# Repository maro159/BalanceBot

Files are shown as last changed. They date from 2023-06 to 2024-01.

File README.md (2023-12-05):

# BalanceBot

RPi Pico based self balancing robot developed as academic project on AGH UST

**NOTE:** This project is still WIP (Work In Progress)

## Overview
A goal was to create two-wheel robot with ability to self-balance. 

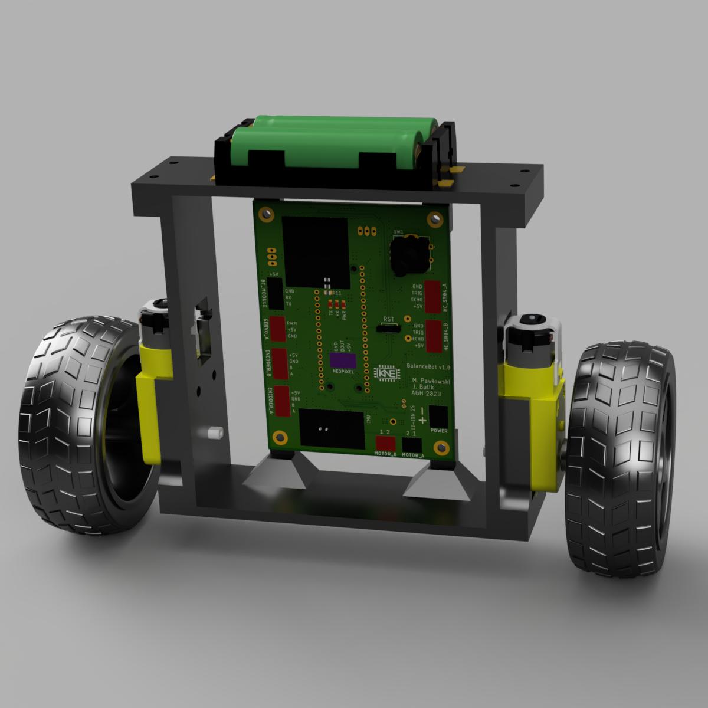
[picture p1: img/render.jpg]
render
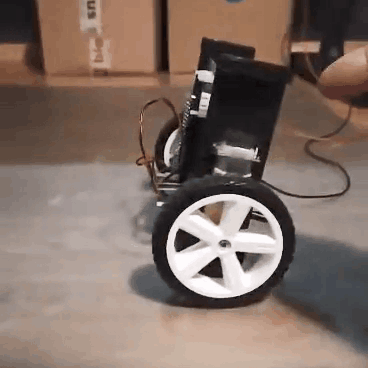
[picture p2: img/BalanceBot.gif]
gif
|  |  |
|-|-|

### Hardware
- 2S LiIon/LiPo battery pack
- custom PCB
- RPi Pico (dual core ARM Cortex M0+)
- DRV8833 H-Bridge (much more efficient than popular L293) 
- 2x DFRobot SJ01 120:1 DC Motor with magnetic encoder
- MPU-6050 6-axis IMU (accelerometer + gyroscope)
- 2x HC04 ultrasonic distance sensor
- SSD1306 OLED display + EC11 rotary encoder 

### Software
Code was written in C language using *Raspberry Pi Pico SDK*.

Self-stabilization algorithm is based on measuring vehicle's tilt angle using accelerometer and gyroscope measurements. The angle is calculated using *complementary filter*. Idea of the filter is to estimate angle avoiding errors from gyroscope low frequency components and accelerometer high frequency components.

Next stage of controller consists of 3-level cascade of PID controllers:

|name|set point|input|output|description|
|-|-|-|-|-|
|pid_speed|target_robot_speed|current_robot_speed|target_angle|calculate angle needed to reach target_robot_speed|
|pid_imu|target_angle|current_angle|target_motor_speed|calculate motor speed needed to reach target_angle|
|pid_motor_a|target_motor_speed|current_motor_a_speed|motor_a_power|calculate power (PWM duty cycle) needed to achieve current_motor_a_speed|
|pid_motor_b|target_motor_speed|current_motor_b_speed|motor_b_power|calculate power (PWM duty cycle) needed to achieve current_motor_b_speed|

This may seem little unintuitive on first sight, but makes robot able to balance "in place" instead of drifting to either side. Such algorithm was possible to implement thanks to motor encoders. Working principle is explained pretty well [on Husarion blog](https://medium.com/husarion-blog/fresh-look-at-self-balancing-robot-algorithm-d50d41711d58), where we got the idea from. Thanks a lot for publishing it!

PID coefficients can be set via OLED GUI, which can be navigated using rotary encoder. Big thanks to David Schramm for the [pico ssd1306 library](https://github.com/daschr/pico-ssd1306)

All of above runs on a single core. There is a plan to use second core for wireless communication and further expand abilities of the robot 

### PC App
There is a [python script](PC/main.py) included, which implements plotting data received on serial port. It is simple and unoptimized, but was really helpful during debugging and tuning of complementary filter and PID controllers.
 
## Further development
- design new frame to lower center of mass -> lower moment of inertia
- replace heavy 18650 LiIon battery pack with light LiPo 
- improve IMU measurements by using MPU-6050's interrupt
- fine-tune PIDs
- implement driving and remote control
- implement obstacle detection using ultrasonic sensors

## Attribution
- *slightly modified* [SSD1306 library by David Schramm](https://github.com/daschr/pico-ssd1306)
- idea of PID cascade from [husarion/self-balancing-telepresence-robot](https://github.com/husarion/self-balancing-telepresence-robot) and [Husarion Medium blog](https://medium.com/husarion-blog/fresh-look-at-self-balancing-robot-algorithm-d50d41711d58)

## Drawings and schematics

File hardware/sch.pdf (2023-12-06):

## IMU

# Power Supply

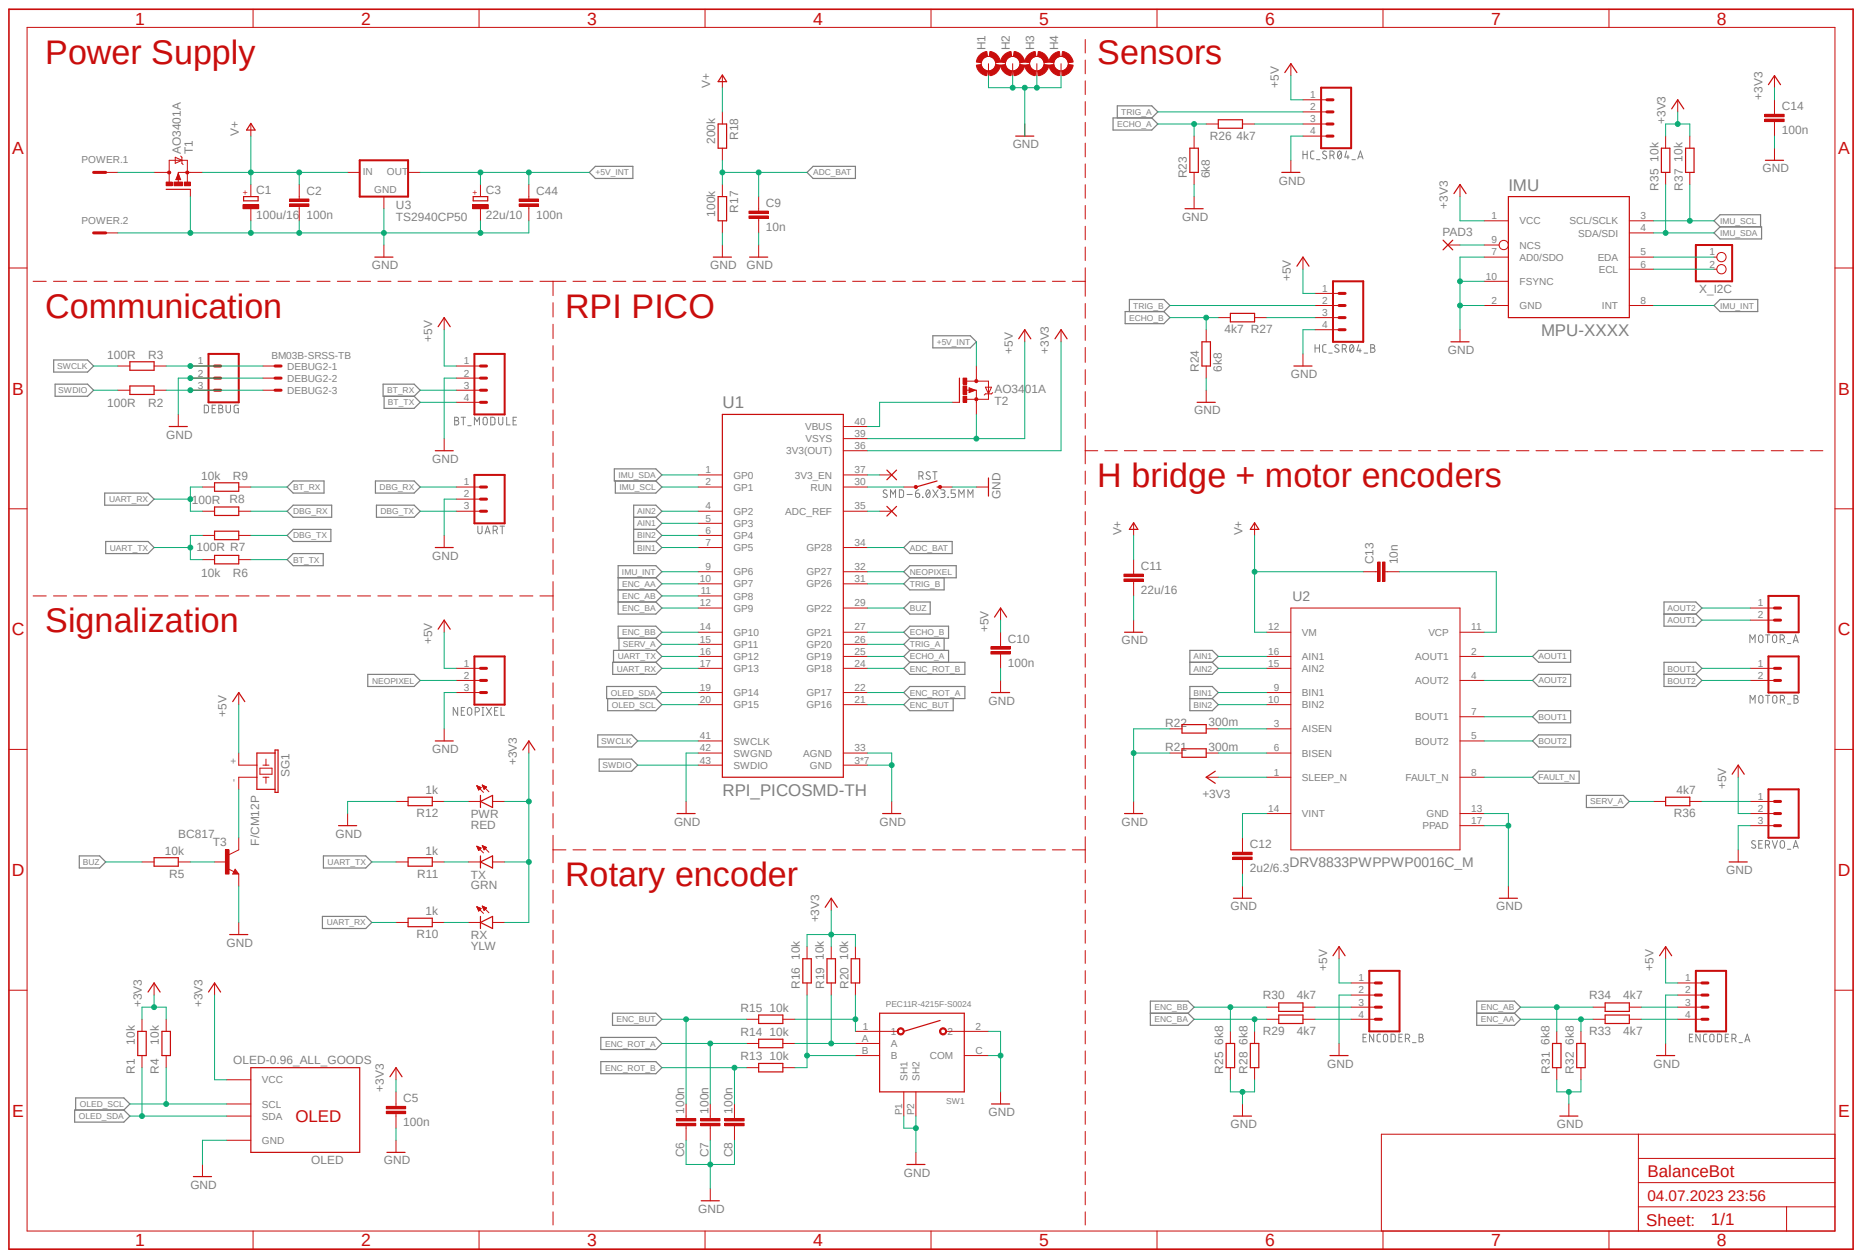
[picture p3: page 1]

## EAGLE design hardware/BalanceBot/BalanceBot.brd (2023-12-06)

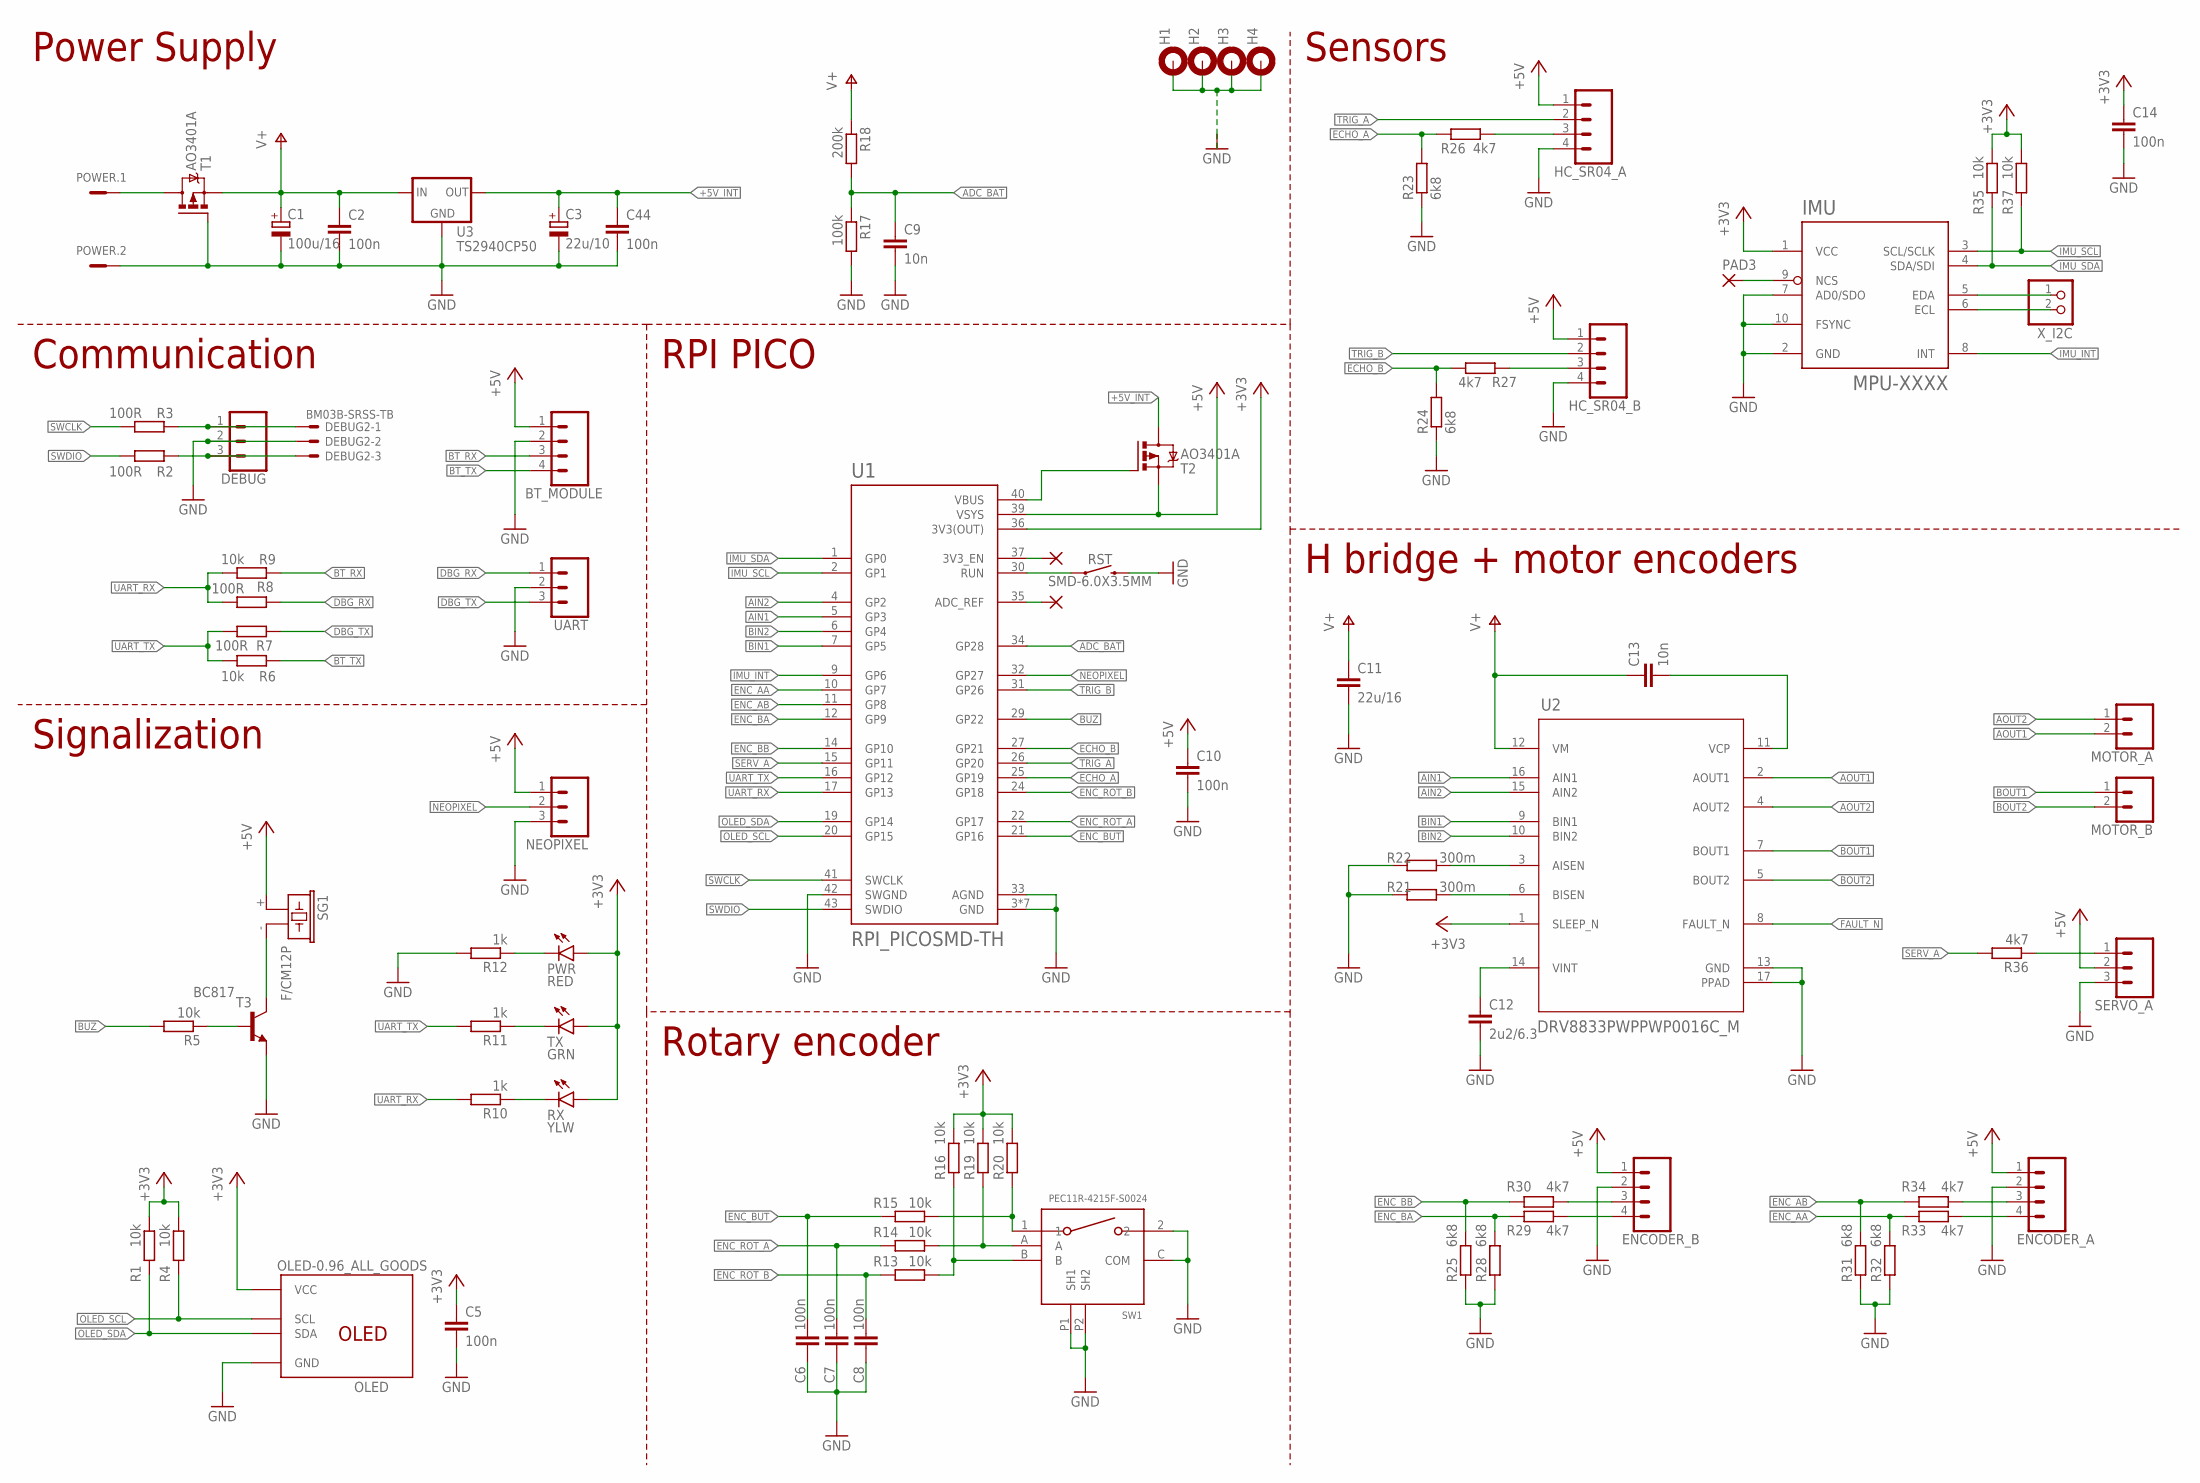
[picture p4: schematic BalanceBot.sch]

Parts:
BT_MODULE: JST-XH-04-PIN-LONG-PAD; JST-XH-04-PACKAGE-LONG-PAD
C1: 100u/16; E2-5
C2, C5, C6, C7, C8, C10, C14, C44: 100n; C0805
C3: 22u/10; SMC_B
C9, C13: 10n; C0805
C11: 22u/16; C0805
C12: 2u2/6.3; C0805
DEBUG: JST-XH-03-PIN-LONG-PAD; JST-XH-03-PACKAGE-LONG-PAD
DEBUG2: BM03B-SRSS-TB
ENCODER_A: JST-XH-04-PIN-LONG-PAD; JST-XH-04-PACKAGE-LONG-PAD
ENCODER_B: JST-XH-04-PIN-LONG-PAD; JST-XH-04-PACKAGE-LONG-PAD
H1, H2, H3, H4: MOUNT-PAD-ROUND3.2; 3,2-PAD
HC_SR04_A, HC_SR04_B: JST-XH-04-PIN-LONG-PAD; JST-XH-04-PACKAGE-LONG-PAD
IMU: MPU-XXXX; MPUXXXX
MOTOR_A: JST-XH-02-PIN-LONG-PAD; JST-XH-02-PACKAGE-LONG-PAD
MOTOR_B: JST-XH-02-PIN-LONG-PAD; JST-XH-02-PACKAGE-LONG-PAD
NEOPIXEL: JST-XH-03-PIN-LONG-PAD; JST-XH-03-PACKAGE-LONG-PAD
OLED: OLED-0.96_ALL_GOODS; ALL_GOODS
PAD1, PAD2, PAD3: WIREPADSMD1,27-254; SMD1,27-2,54
POWER: MCV2
PWR: RED; CHIP-LED0805
R1, R4, R5, R6, R9, R13, R14, R15, R16, R19, R20, R35, R37: 10k; R0805
R2, R3, R7, R8: 100R; R0805
R10, R11, R12: 1k; R0805
R17: 100k; R0805
R18: 200k; R0805
R21, R22: 300m; R1206
R23, R24, R25, R28, R31, R32: 6k8; R0805
R26, R27, R29, R30, R33, R34, R36: 4k7; R0805
RST: SMD-6.0X3.5MM; TACTILE_SWITCH_SMD_6.0X3.5MM
RX: YLW; CHIP-LED0805
SERVO_A: JST-XH-03-PIN-LONG-PAD; JST-XH-03-PACKAGE-LONG-PAD
SG1: F/CM12P
SW1: PEC11R-4215F-S0024
T1, T2: AO3401A; SOT23
T3: BC817; SOT23-BEC
TX: GRN; CHIP-LED0805
U1: RPI_PICOSMD-TH; PICO-PKG-TH-ONLY
U2: DRV8833PWPPWP0016C_M; PWP0016C_M
U3: TS2940CP50; DPACK
UART: JST-XH-03-PIN-LONG-PAD; JST-XH-03-PACKAGE-LONG-PAD
X_I2C: PINHD-1X2; 1X02

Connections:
3V3_EN: PAD2.1, U1.37 (3V3_EN)
+3V3: C5.1, C14.1, IMU.1 (VCC), OLED.2 (VCC), PWR.A, R1.1, R4.1, R16.1, R19.1, R20.1, R35.1, R37.1, RX.A, TX.A, U1.36 (3V3(OUT)), U2.1 (SLEEP_N)
+5V: BT_MODULE.1, C10.1, ENCODER_A.1, ENCODER_B.1, HC_SR04_A.1, HC_SR04_B.1, NEOPIXEL.1, SERVO_A.2, SG1.+ (1), T2.2 (S), U1.39 (VSYS)
+5V_INT: C3.+, C44.1, T2.3 (D), U3.3 (OUT)
ADC_BAT: C9.1, R17.1, R18.2, U1.34 (GP28)
ADC_REF: PAD1.1, U1.35 (ADC_REF)
AIN1: U1.5 (GP3), U2.16 (AIN1)
AIN2: U1.4 (GP2), U2.15 (AIN2)
AOUT1: MOTOR_A.2, U2.2 (AOUT1)
AOUT2: MOTOR_A.1, U2.4 (AOUT2)
BIN1: U1.7 (GP5), U2.9 (BIN1)
BIN2: U1.6 (GP4), U2.10 (BIN2)
BOUT1: MOTOR_B.1, U2.7 (BOUT1)
BOUT2: MOTOR_B.2, U2.5 (BOUT2)
BT_RX: BT_MODULE.3, R9.1
BT_TX: BT_MODULE.4, R6.1
BUZ: R5.2, U1.29 (GP22)
DBG_RX: R8.1, UART.1
DBG_TX: R7.1, UART.3
ECHO_A: R23.2, R26.1, U1.25 (GP19)
ECHO_B: R24.2, R27.1, U1.27 (GP21)
ECL: IMU.6 (ECL), X_I2C.2
EDA: IMU.5 (EDA), X_I2C.1
ENC_AA: R32.2, R33.1, U1.10 (GP7)
ENC_AB: R31.2, R34.2, U1.11 (GP8)
ENC_BA: R28.2, R29.1, U1.12 (GP9)
ENC_BB: R25.2, R30.2, U1.14 (GP10)
ENC_BUT: C6.1, R15.1, U1.21 (GP16)
ENC_ROT_A: C7.1, R14.1, U1.22 (GP17)
ENC_ROT_B: C8.1, R13.1, U1.24 (GP18)
FAULT_N: U2.8 (FAULT_N)
GND: BT_MODULE.2, C1.-, C2.2, C3.-, C5.2, C6.2, C7.2, C8.2, C9.2, C10.2, C11.2, C12.2, C14.2, C44.2, DEBUG.2, DEBUG2.2, ENCODER_A.2, ENCODER_B.2, H1.B3,2, H2.B3,2, H3.B3,2, H4.B3,2, HC_SR04_A.4, HC_SR04_B.4, IMU.2 (GND), IMU.7 (AD0/SDO), IMU.10 (FSYNC), NEOPIXEL.3, OLED.1 (GND), POWER.2, R12.2, R17.2, R21.1, R22.1, R23.1, R24.1, R25.1, R28.1, R31.1, R32.1, RST.2, SERVO_A.3, SW1.2, SW1.C (COM), SW1.P1 (SH1), SW1.P2 (SH2), T1.1 (G), T3.E, U1.3 (GND), U1.8 (GND), U1.13 (GND), U1.18 (GND), U1.23 (GND), U1.28 (GND), U1.33 (AGND), U1.38 (GND), U1.42 (SWGND), U2.13 (GND), U2.17 (PPAD), U3.4 (GND), UART.2
IMU_INT: IMU.8 (INT), U1.9 (GP6)
IMU_SCL: IMU.3 (SCL/SCLK), R37.2, U1.2 (GP1)
IMU_SDA: IMU.4 (SDA/SDI), R35.2, U1.1 (GP0)
unnamed: R22.2, U2.3 (AISEN)
unnamed: R21.2, U2.6 (BISEN)
unnamed: C13.2, U2.11 (VCP)
unnamed: C12.1, U2.14 (VINT)
unnamed: POWER.1, T1.3 (D)
unnamed: PWR.C, R12.1
unnamed: R11.1, TX.C
unnamed: R15.2, R20.2, SW1.1
unnamed: R5.1, T3.B
unnamed: R14.2, R19.2, SW1.A
unnamed: SG1.- (2), T3.C
unnamed: R13.2, R16.2, SW1.B
unnamed: R10.1, RX.C
unnamed: HC_SR04_A.3, R26.2
unnamed: HC_SR04_B.3, R27.2
unnamed: ENCODER_A.3, R34.1
unnamed: ENCODER_A.4, R33.2
unnamed: ENCODER_B.3, R30.1
unnamed: ENCODER_B.4, R29.2
unnamed: DEBUG.1, DEBUG2.1, R3.1
unnamed: R36.1, SERVO_A.1
unnamed: DEBUG.3, DEBUG2.3, R2.2
NCS: IMU.9 (NCS), PAD3.1
NEOPIXEL: NEOPIXEL.2, U1.32 (GP27)
OLED_SCL: OLED.3 (SCL), R4.2, U1.20 (GP15)
OLED_SDA: OLED.4 (SDA), R1.2, U1.19 (GP14)
RUN: RST.1, U1.30 (RUN)
SERV_A: R36.2, U1.15 (GP11)
SWCLK: R3.2, U1.41 (SWCLK)
SWDIO: R2.1, U1.43 (SWDIO)
TRIG_A: HC_SR04_A.2, U1.26 (GP20)
TRIG_B: HC_SR04_B.2, U1.31 (GP26)
UART_RX: R8.2, R9.2, R10.2, U1.17 (GP13)
UART_TX: R6.2, R7.2, R11.2, U1.16 (GP12)
V+: C1.+, C2.1, C11.1, C13.1, R18.1, T1.2 (S), U2.12 (VM), U3.1 (IN)
VBUS: T2.1 (G), U1.40 (VBUS)

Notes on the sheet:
RPI PICO
Power Supply
Communication
Signalization
Rotary encoder
H bridge + motor encoders
Sensors

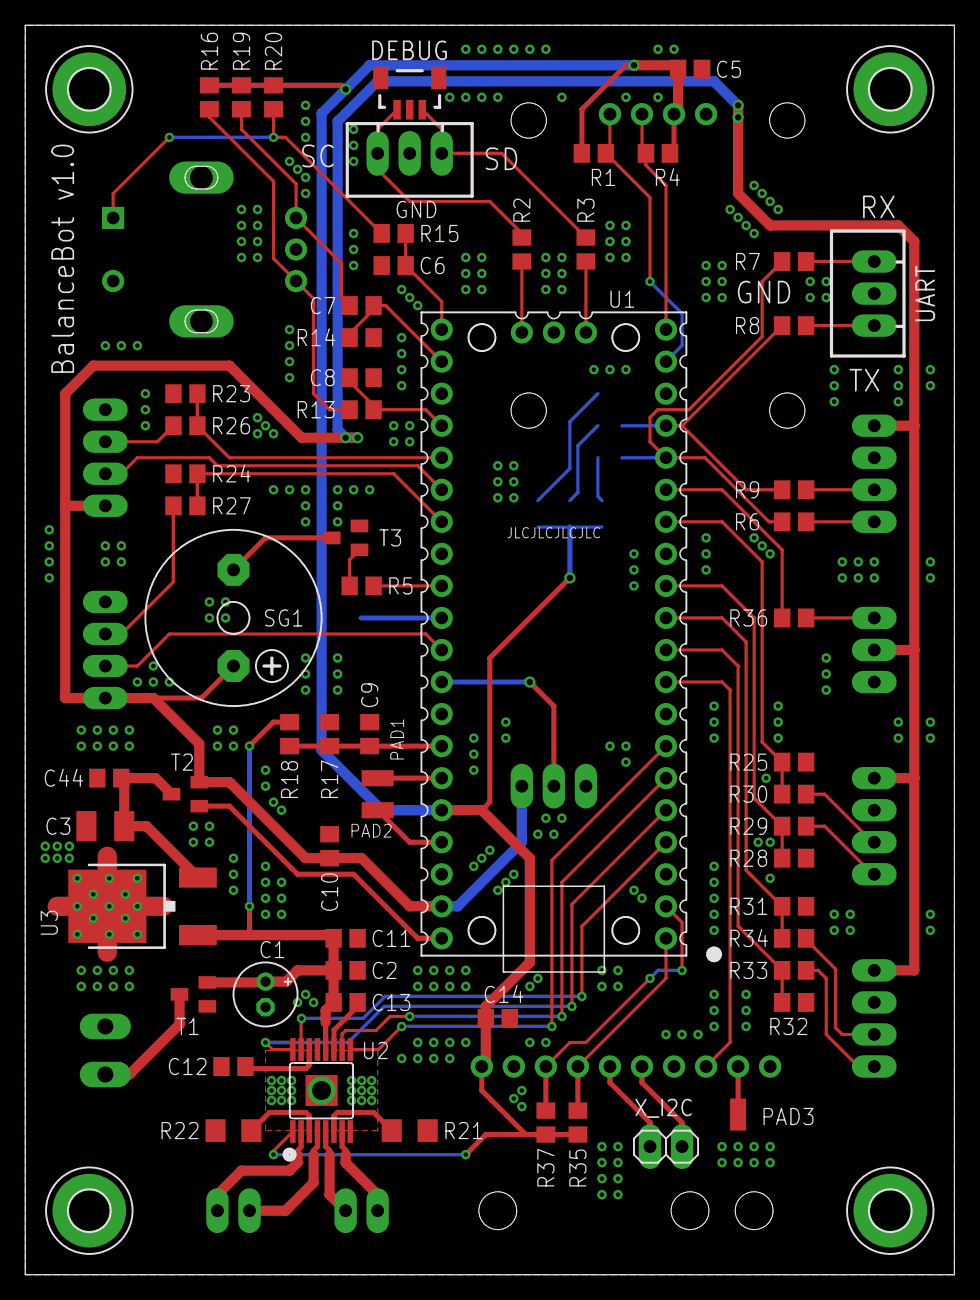
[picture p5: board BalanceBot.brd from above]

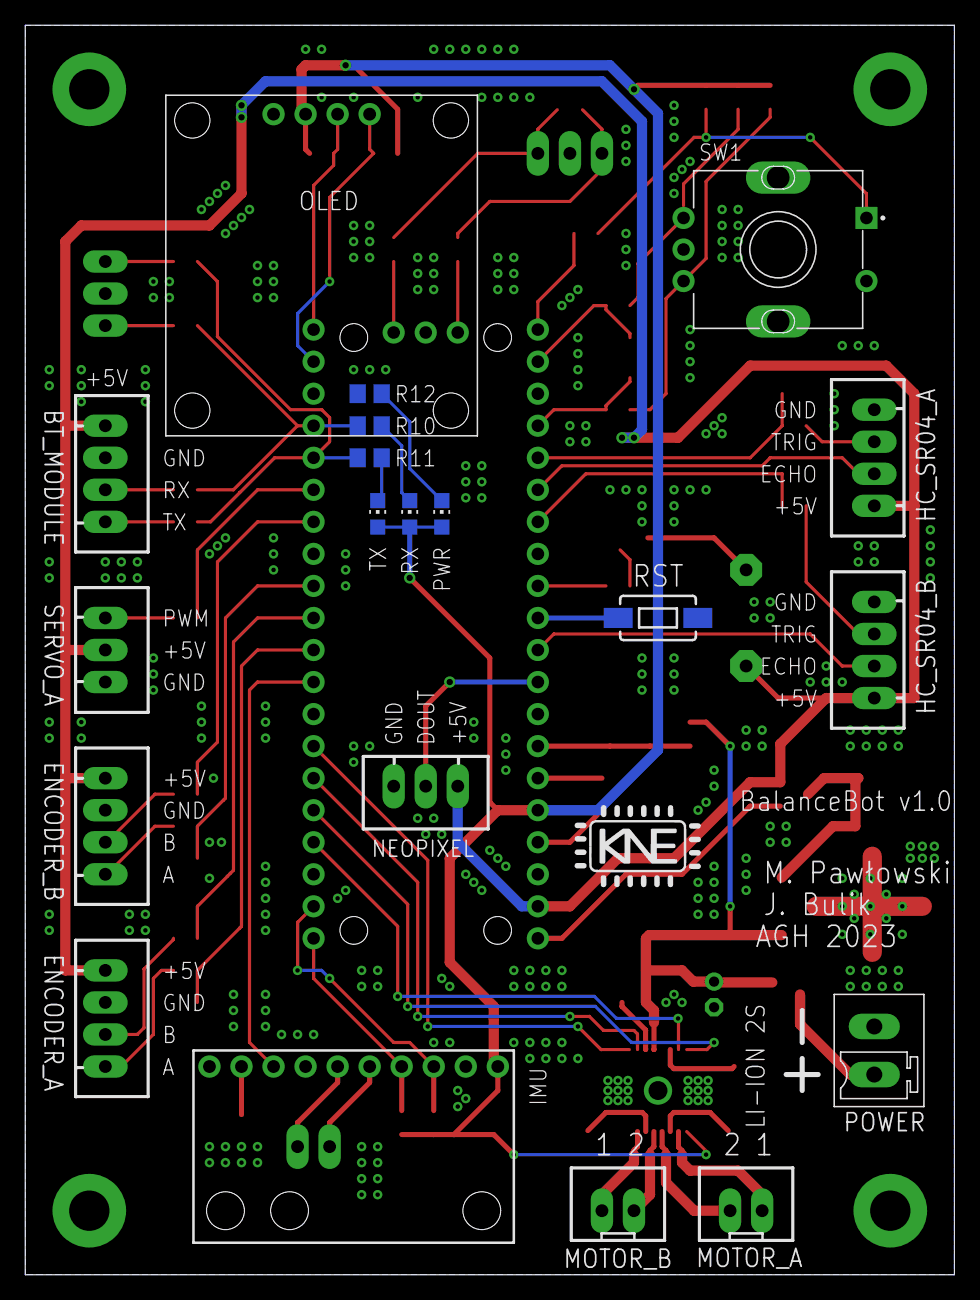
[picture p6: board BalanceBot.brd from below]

Board: 2 copper layers, 73.7 x 99.1 mm, 86 parts (20 on the bottom side), 70 nets.

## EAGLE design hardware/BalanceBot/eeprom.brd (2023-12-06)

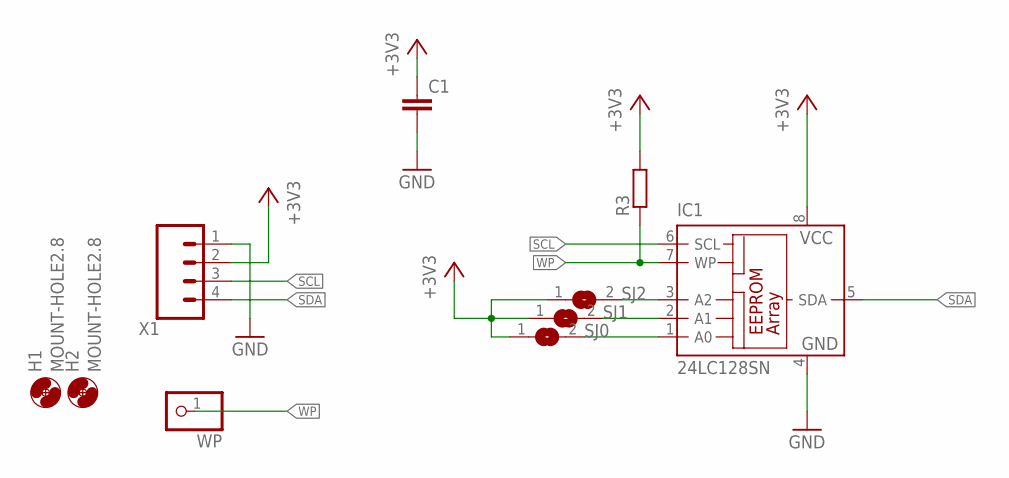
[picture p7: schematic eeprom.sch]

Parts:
C1: C-EUC0805; C0805
H1, H2: MOUNT-HOLE2.8; 2,8
IC1: 24LC128SN; SO-08
R3: R-EU_R0805; R0805
SJ0, SJ1, SJ2: SJ
WP: PINHD-1X1; 1X01
X1: JST-XH-04-PIN-ROUND-PAD; JST-XH-04-PACKAGE-ROUND-PAD

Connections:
+3V3: C1.1, IC1.8 (VCC), R3.2, SJ0.1, SJ1.1, SJ2.1, X1.2
GND: C1.2, IC1.4 (GND), X1.1
unnamed: IC1.3 (A2), SJ2.2
unnamed: IC1.2 (A1), SJ1.2
unnamed: IC1.1 (A0), SJ0.2
SCL: IC1.6 (SCL), X1.3
SDA: IC1.5 (SDA), X1.4
WP: IC1.7 (WP), R3.1, WP.1

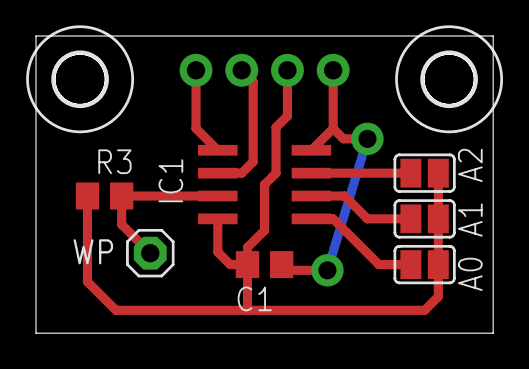
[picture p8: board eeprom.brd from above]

Board: 2 copper layers, 25.4 x 16.5 mm, 10 parts (1 on the bottom side), 8 nets.

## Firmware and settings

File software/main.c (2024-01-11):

#include <string.h>
#include <stdlib.h>
#include <stdio.h>
#include <stdlib.h>
#include <string.h>
#include "pico/stdlib.h"
#include "hardware/uart.h"
#include "hardware/gpio.h"
#include "hardware/divider.h"
#include "hardware/i2c.h"
#include "hardware/pio.h"
#include "hardware/timer.h"
#include "hardware/watchdog.h"
#include "hardware/clocks.h"
#include "hardware/adc.h"
#include "pins.h"
#include "motor.h"
#include "oled.h"
#include "encoder_rot.h"
#include "menu.h"
#include "imu.h"
#include "controler.h"

static volatile bool time_to_go = false; 
const uint32_t sampling_time_us = 10 * 1000;
uint32_t last_time_us = 0;

static void init()
{
    i2c_init(IMU_I2C, IMU_BAUDRATE);  
    gpio_set_function(IMU_SDA, GPIO_FUNC_I2C);
    gpio_set_function(IMU_SCL, GPIO_FUNC_I2C);
    gpio_init(IMU_INT);
    gpio_set_dir(IMU_INT, false);

    i2c_init(OLED_I2C, OLED_BAUDRATE);
    gpio_set_function(OLED_SDA, GPIO_FUNC_I2C);
    gpio_set_function(OLED_SCL, GPIO_FUNC_I2C);
    
    gpio_set_function(MOTOR_A1, GPIO_FUNC_PWM);
    gpio_set_function(MOTOR_A2, GPIO_FUNC_PWM);
    gpio_set_function(MOTOR_B1, GPIO_FUNC_PWM);
    gpio_set_function(MOTOR_B2, GPIO_FUNC_PWM);

    gpio_set_function(SERWO, GPIO_FUNC_PWM);

    // uart_init(BT_UART, BT_BAUDRATE);
    stdio_uart_init_full(BT_UART, BT_BAUDRATE, BT_TX, BT_RX);
    // stdio_init_all();
    gpio_set_function(BT_TX, GPIO_FUNC_UART);
    gpio_set_function(BT_RX, GPIO_FUNC_UART);
    
    adc_init();
    adc_gpio_init(BATTERY_LVL);
    adc_select_input(BATTERY_LVL_ADC);
        
    gpio_init(HC04_A_TRIG);
    gpio_init(HC04_B_TRIG); 
    gpio_set_dir(HC04_A_TRIG, true);
    gpio_set_dir(HC04_B_TRIG, true);

    gpio_init(HC04_A_ECHO);
    gpio_init(HC04_B_ECHO); 
    gpio_set_dir(HC04_A_ECHO, false);
    gpio_set_dir(HC04_B_ECHO, false);

    gpio_init(BUZZ); 
    gpio_set_dir(BUZZ, true);

    gpio_init(NEOPX); 
    gpio_set_dir(NEOPX, true);

    gpio_init(ENC_ROT_A);
    gpio_init(ENC_ROT_B);
    gpio_init(ENC_ROT_SW); 
    gpio_set_dir(ENC_ROT_A, false);
    gpio_set_dir(ENC_ROT_B, false);
    gpio_set_dir(ENC_ROT_SW, false);
}

bool controler_timer_callback(repeating_timer_t *t)
{
    time_to_go = true; 
    return true; //to continue repeating 
}

int main() 
{
    bool is_run = false;
    bool was_run = false;

    repeating_timer_t controler_timer;
    init();
    init_motor();
    // init_servo();
    init_oled();
    init_encoder();
    init_imu();
    init_controler(sampling_time_us);
    init_menu();
    /* Negative delay so means we will call repeating_timer_callback, and call it again 
     * regardless of how long the callback took to execute */
    add_repeating_timer_us(-(int64_t)(sampling_time_us), &controler_timer_callback, NULL, &controler_timer); 
    while(true)
    {
        if(time_to_go)
        {
            uint32_t current_time_us = time_us_32();
            uint32_t dt_us = current_time_us - last_time_us;
            last_time_us = current_time_us;
            // printf("*%u\n*",dt_us);
            controler_update();
            // printf("*%u\n*",time_us_32()-last_time_us);
            printf("%f,%f,%f,%f,%f,%f\n",*pid_speed->setpoint, *pid_speed->input, *pid_imu->setpoint, *pid_imu->input, *pid_motor_a->setpoint, *pid_motor_a->input);
            
            time_to_go = false;
        }
        if(menu_get() == &menu_run) is_run = true;
        else is_run = false;

        if(!was_run && is_run) controler_run();
        else if(was_run && !is_run) controler_stop();
        was_run = is_run;
    }
}

/*
int main()
{    
    Init();
    init_motor();
    const uint32_t timeout_us = 1000;
    uint8_t buf[30];
    uint32_t buf_head = 0;
    Motor motor = MOTOR_A;

    while(true)
    {
        int c = getchar_timeout_us(timeout_us);	
        if (c != PICO_ERROR_TIMEOUT)
        {
            buf[buf_head++] = c;
            if (c == 0x0D)
            {
                
                // Convert the uint8_t array to a string
                char str[buf_head];
                strncpy(str, (char*)buf, buf_head);
                str[buf_head] = '\0';
                printf(str);
                // Convert the string to an integer
                int value = atoi(str);
                printf("Converted: %d", value);
                bool direction = DIR_FORWARD;
                uint32_t pwm = convert_pwm(value, &direction);
                printf("Value: %d, direction: %d", pwm, direction);
                // motor_set_speed(motor, pwm, direction);
                buf_head = 0;
            }
            else if (c == 'A')
            {
                motor = MOTOR_A;
                printf("Motor A\n");
                buf_head=0;
            }
            else if (c == 'B')
            {
                motor = MOTOR_B;
                printf("Motor B\n");
                buf_head=0;
            }
        }
        
    }
    

    return 0;
}*/

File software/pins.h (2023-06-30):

#ifndef _PINS_H_
#define _PINS_H_

// #define DEBUG_MODE

#define IMU_SDA 0
#define IMU_SCL 1
#define IMU_INT 6
#define IMU_I2C i2c0
#define IMU_BAUDRATE 400*1000

#define OLED_SDA 14
#define OLED_SCL 15
#define OLED_I2C i2c1
#define OLED_BAUDRATE 400*1000

#define BT_TX 12
#define BT_RX 13
#define BT_UART uart0
#define BT_BAUDRATE 115200

#define SERWO 11 
#define SERWO_SLICE 5
#define SERWO_CHAN PWM_CHAN_B

#define MOTOR_A1 3
#define MOTOR_A2 2
#define MOTOR_B1 5
#define MOTOR_B2 4
#define MOTOR_A_SLICE 1
#define MOTOR_A1_CHAN PWM_CHAN_B
#define MOTOR_A2_CHAN PWM_CHAN_A
#define MOTOR_B_SLICE 2
#define MOTOR_B1_CHAN PWM_CHAN_B
#define MOTOR_B2_CHAN PWM_CHAN_A

#define MOTOR_ENC_AA 7
#define MOTOR_ENC_AB 8
#define MOTOR_ENC_BA 9
#define MOTOR_ENC_BB 10

#define ENC_ROT_A 17
#define ENC_ROT_B 18
#define ENC_ROT_SW 16

#define HC04_A_TRIG 20
#define HC04_B_TRIG 26
#define HC04_A_ECHO 19
#define HC04_B_ECHO 21

#define BUZZ 22
#define NEOPX 27 // albo EEPROM_WP

#define BATTERY_LVL 28
#define BATTERY_LVL_ADC 2 // adc channel 


#endif

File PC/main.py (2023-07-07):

import serial
import time
import threading
import matplotlib.pyplot as plt
from collections import deque


class SerialReader:
    def __init__(self, port):
        self.port = port
        self.ser = None
        self.is_running = False
        self.data1 = deque(maxlen=1000)
        self.data2 = deque(maxlen=1000)
        self.data3 = deque(maxlen=1000)
        self.data4 = deque(maxlen=1000)
        self.data5 = deque(maxlen=1000)
        self.data6 = deque(maxlen=1000)
        self.lock = threading.Lock()

    def start(self):
        self.ser = serial.Serial(self.port, baudrate=115200)
        self.is_running = True
        self.read_data()

    def stop(self):
        self.is_running = False
        if self.ser:
            self.ser.close()

    def read_data(self):
        while self.is_running:
            try:
                line = self.ser.readline().decode('utf-8').strip()
                values = line.split(',')
                if len(values) == 6:
                    pid_speed_set = float(values[0])
                    pid_speed_in = float(values[1])
                    pid_imu_set = float(values[2])
                    pid_imu_in = float(values[3])
                    pid_motor_set = float(values[4])
                    pid_motor_in = float(values[5])
                    with self.lock:
                        self.data1.append(pid_speed_set)
                        self.data2.append(pid_speed_in)
                        self.data3.append(pid_imu_set)
                        self.data4.append(pid_imu_in)
                        self.data5.append(pid_motor_set)
                        self.data6.append(pid_motor_in)
            except (UnicodeDecodeError, ValueError):
                pass

    def get_data(self):
        with self.lock:
            return (
                list(self.data1),
                list(self.data2),
                list(self.data3),
                list(self.data4),
                list(self.data5),
                list(self.data6),
            )


class Plotter:
    def __init__(self, reader):
        self.reader = reader
        self.is_running = False
        self.fig, (self.ax1, self.ax2, self.ax3) = plt.subplots(3, 1, sharex="all")
        self.line1, = self.ax1.plot([], label='set point')
        self.line2, = self.ax1.plot([], label='input')
        self.line3, = self.ax2.plot([], label='set point')
        self.line4, = self.ax2.plot([], label='input')
        self.line5, = self.ax3.plot([], label='set point')
        self.line6, = self.ax3.plot([], label='input')
        self.update_interval = 0.05  # Update plot every 0.1 seconds (10 times per second)
        self.lock = threading.Lock()

        # Set titles for subplots
        self.ax1.set_title('PID Speed')
        self.ax2.set_title('PID IMU')
        self.ax3.set_title('PID Motor')

    def start(self):
        self.is_running = True
        self.plot_data_thread()

    def stop(self):
        self.is_running = False

    def plot_data_thread(self):
        while self.is_running:
            (
                data1,
                data2,
                data3,
                data4,
                data5,
                data6,
            ) = self.reader.get_data()
            with self.lock:
                self.line1.set_data(range(len(data1)), data1)
                self.line2.set_data(range(len(data2)), data2)
                self.line3.set_data(range(len(data3)), data3)
                self.line4.set_data(range(len(data4)), data4)
                self.line5.set_data(range(len(data5)), data5)
                self.line6.set_data(range(len(data6)), data6)

            self.ax1.relim()
            self.ax1.autoscale_view(scaley=True)
            self.ax2.relim()
            self.ax2.autoscale_view(scaley=True)
            self.ax3.relim()
            self.ax3.autoscale_view(scaley=True)
            self.ax1.legend(loc='upper right', bbox_to_anchor=(1, 1))
            self.ax2.legend(loc='upper right', bbox_to_anchor=(1, 1))
            self.ax3.legend(loc='upper right', bbox_to_anchor=(1, 1))

            self.fig.canvas.draw()
            time.sleep(self.update_interval)

    def show_plot(self):
        self.ax1.legend()
        self.ax2.legend()
        self.ax3.legend()
        plt.subplots_adjust(hspace=0.4)  # Adjust vertical spacing between subplots
        plt.show()


def main():
    reader = SerialReader('COM10')
    plotter = Plotter(reader)

    reader_thread = threading.Thread(target=reader.start)
    plotter_thread = threading.Thread(target=plotter.start)

    reader_thread.start()
    plotter_thread.start()

    try:
        plotter.show_plot()
    except KeyboardInterrupt:
        pass
    finally:
        reader.stop()
        plotter.stop()
        reader_thread.join()
        plotter_thread.join()


if __name__ == '__main__':
    main()

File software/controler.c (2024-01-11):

#include "pico/stdlib.h"
#include "controler.h"
#include "pins.h"
#include "imu.h"
#include "pid.h"
#include "motor.h"

static float sampling_time_sec;

static float acc_angle_deg = 0.0;
static float gyro_angular = 0.0;

static float last_speeds[30] = {0};
static uint32_t last_speeds_head = 0;

static float current_robot_speed = 0.0;
float target_robot_speed = 0.0; // for remote control

float zero_angle = 8.0; // global
static float target_angle = 0.0;
static float target_angle_offset = 0.0;

static float current_angle = 0.0;
static float target_motors_speed = 0.0;   

static float current_motor_a_speed = 0.0;
static float motor_a_power = 0.0;                

static float current_motor_b_speed = 0.0;
static float motor_b_power = 0.0;   

static struct pid_controller pid_speed_ctrl;
static struct pid_controller pid_imu_ctrl;
static struct pid_controller pid_motor_a_ctrl;
static struct pid_controller pid_motor_b_ctrl;

pid_ctrl pid_speed;
pid_ctrl pid_imu;
pid_ctrl pid_motor_a;
pid_ctrl pid_motor_b;

static int32_t motor_a_enc_last = 0; 
static int32_t motor_b_enc_last = 0; 


/*
            pid_speed                   pid_imu                 pid_motor_a                 pid_motor_b
in          &current_robot_speed        &current_angle          &current_motor_a_speed      &current_motor_b_speed
out         &target_angle               &target_motor_speed     &motor_a_power              &motor_a_power
set         &target_robotspeed          &target_angle           &target_motor_speed         &target_motor_speed

*/

static void _refresh_data() 
{
    // TODO: make independent from sampling timer
    // parameter used in complementary filter. Pretty much dependent on sampling time.
    float alpha = 0.990;
    // float alpha = 0.990;

    motor_encoder_request();
    imu_get_data(&acc_angle_deg, &gyro_angular);
    
    int32_t motor_a_enc = motor_encoder_fetch(MOTOR_A);
    int32_t motor_b_enc = motor_encoder_fetch(MOTOR_B);

    /* unit of motor speed is 4 * rps (rotates per second)
     * could be divided by 4 but is not
     */
    current_motor_a_speed = (motor_a_enc - motor_a_enc_last) / (MOTOR_ENCODER_TICKS * sampling_time_sec);
    current_motor_b_speed = (motor_b_enc - motor_b_enc_last) / (MOTOR_ENCODER_TICKS * sampling_time_sec);
    #if ENC_A_INVERT==1
    current_motor_a_speed = -current_motor_a_speed;
    #endif
    #if ENC_B_INVERT==1
    current_motor_b_speed = -current_motor_b_speed;
    #endif

    // implementation of complementary filter to obtain reliable angle
    current_angle = alpha * (current_angle + sampling_time_sec * gyro_angular) + (1 - alpha) * acc_angle_deg;
    // current_angle = (current_angle + sampling_time_sec * gyro_angular);  // gyroscope-only angle 
    // current_angle = alpha * current_angle + (1 - alpha) * acc_angle_deg; // accelerometer-only angle


    /* robot speed is calculated as moving average to achieve smooth control */
    current_robot_speed = (current_motor_a_speed + current_motor_b_speed) / 2.0;
    last_speeds[last_speeds_head++] = current_robot_speed;
    if(last_speeds_head >= sizeof(last_speeds)/sizeof(last_speeds[0])) last_speeds_head = 0;

    current_robot_speed = 0;
    for(uint32_t i = 0; i < sizeof(last_speeds)/sizeof(last_speeds[0]); i++)
    {
        current_robot_speed += last_speeds[i];
    }
    current_robot_speed /= sizeof(last_speeds)/sizeof(last_speeds[0]);
    motor_a_enc_last = motor_a_enc;
    motor_b_enc_last = motor_b_enc;
}

void init_controler(uint32_t sampling_time_us)
{   
    sampling_time_sec = sampling_time_us / (1000000.0);
    float kp_speed = 3.0;
    float ki_speed = 3.0;
    float kd_speed = 0.080;

    float kp_imu = 5.0;
    float ki_imu = 0.0;
    float kd_imu = 0.080;

    float kp_motor = 0.2;
    float ki_motor = 0.0;
    float kd_motor = 0.0;

    pid_speed = pid_create(&pid_speed_ctrl, &current_robot_speed, &target_angle_offset, &target_robot_speed, kp_speed, ki_speed, kd_speed); 
    pid_imu = pid_create(&pid_imu_ctrl, &current_angle, &target_motors_speed, &target_angle, kp_imu, ki_imu, kd_imu);
    pid_motor_a = pid_create(&pid_motor_a_ctrl, &current_motor_a_speed, &motor_a_power, &target_motors_speed, kp_motor, ki_motor, kd_motor);
    pid_motor_b = pid_create(&pid_motor_b_ctrl, &current_motor_b_speed, &motor_b_power, &target_motors_speed, kp_motor, ki_motor, kd_motor);

    pid_sample(pid_speed, sampling_time_us);
    pid_sample(pid_imu, sampling_time_us);
    pid_sample(pid_motor_a, sampling_time_us);
    pid_sample(pid_motor_b, sampling_time_us);

    pid_limits(pid_speed, -10, 10); // max angle offset to achieve speed
    pid_limits(pid_imu, -10, 10);   // max motor speed
    pid_limits(pid_motor_a, -1, 1); // max motor a power
    pid_limits(pid_motor_b, -1, 1); // max motor b power

    _refresh_data();
    current_angle = acc_angle_deg;  // initial angle from accelerometer

}
 
void controler_update()
{
    _refresh_data();
    int32_t current_angle_int = (int32_t)(current_angle);
    if(current_angle_int > 45 || current_angle_int < -45) controler_stop();
    pid_compute(pid_speed);     // compute angle offset to achieve target speed
    target_angle = zero_angle - target_angle_offset;
    pid_compute(pid_imu);       // compute motor speed to achieve target angle 
    pid_compute(pid_motor_a);   // compute motor power (pwm) to achieve target speed
    pid_compute(pid_motor_b);   // compute motor power (pwm) to achieve target speed
    motor_a_power = target_motors_speed * 0.1;  // TODO: use pid instead
    motor_b_power = target_motors_speed * 0.1;  // TODO: use pid instead
    motor_set_power(MOTOR_A,motor_a_power);
    motor_set_power(MOTOR_B,motor_b_power);
}

void controler_stop()
{
    // disable pids, and set outputs to 0
    pid_set_mode(pid_speed, E_MODE_MANUAL);
    pid_set_mode(pid_imu, E_MODE_MANUAL);
    pid_set_mode(pid_motor_a, E_MODE_MANUAL);
    pid_set_mode(pid_motor_b, E_MODE_MANUAL);
    *pid_speed->output = 0;
    *pid_imu->output = 0;
    *pid_motor_a->output = 0;
    *pid_motor_b->output = 0;
    // TODO: parking
}

void controler_run()
{
    // set pids coeffs which may changed in menu
    pid_tune(pid_speed, pid_speed->kp_disp, pid_speed->ki_disp, pid_speed->kd_disp);
    pid_tune(pid_imu, pid_imu->kp_disp, pid_imu->ki_disp, pid_imu->kd_disp);
    pid_tune(pid_motor_a, pid_motor_a->kp_disp, pid_motor_a->ki_disp, pid_motor_a->kd_disp);
    pid_tune(pid_motor_b, pid_motor_a->kp_disp, pid_motor_a->ki_disp, pid_motor_a->kd_disp);

    // turn on pids
    pid_set_mode(pid_speed, E_MODE_AUTO);
    pid_set_mode(pid_imu, E_MODE_AUTO);
    // pid_set_mode(pid_motor_a, E_MODE_AUTO);
    // pid_set_mode(pid_motor_b, E_MODE_AUTO);
}

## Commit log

2023-06-17 add arm gcc kit
2023-06-18 add motor support
2023-06-21 menu prototype add
2023-06-22 improve menu and encoder
2023-06-23 add pid support
2023-06-25 modyfing controler ,motor, timer
2023-06-26 add static keywords, fix timer
    [controler.c, encoder_rot.c, oled.c]
2023-06-27 improvement of pids and motors
2023-07-02 improve controler & encoder
2023-07-07 small fixes
    invert logo
    inverse encoder of motor B
    add pc data visualizer
    [main.py, motor.h]
2023-12-06 add pcb files
    [BalanceBot.brd, BalanceBot.sch, eeprom.brd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]
2024-01-11 refactor code
    - remove global variables from imu.c/imu.h
    - rename motor motor_encoder_get to motor_encoder_fetch
    - fix pid menu entries
    - set sample time in main.c only
    [controler.c, imu.c, main.c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]
2024-01-11 fall detection
    stop motors when angle > 45

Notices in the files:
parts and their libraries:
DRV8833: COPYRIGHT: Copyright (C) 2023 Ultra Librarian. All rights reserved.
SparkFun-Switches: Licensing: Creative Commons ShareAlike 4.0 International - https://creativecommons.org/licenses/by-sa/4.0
